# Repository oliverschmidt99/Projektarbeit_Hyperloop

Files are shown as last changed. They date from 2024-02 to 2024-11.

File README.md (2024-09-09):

# Hyperloop

Hyperloop-Projektarbeit an der Hochschule Emden/Leer

## Installiere MATLAB und das IO-Blockset von Speedgoat.

### Linux

#### Installation von Matlab
Lade [Matlab](https://de.mathworks.com/downloads/) herunter. Erstelle ein Verzeichnis an einen beliebigen Ort und Entpacke die Datei und führe die folgenden Befehle aus.

```bash
xhost +SI:localuser:root 
sudo -H ./install 
xhost -SI:localuser:root
```

#### Installation des IO-Blocksets von Speedgoat

Nach der Installation von MATLAB muss das IO-Blockset von Speedgoat installiert werden. Dafür ist es erforderlich, einen Account bei Speedgoat zu erstellen, um Zugriff auf die [Blockset-Dateien](https://www.speedgoat.com/extranet#/Downloads) zu erhalten.

Lade die ZIP-Datei herunter und entpacke sie in dasselbe Verzeichnis, in dem MATLAB installiert wurde.

Anschließend muss in MATLAB über den internen Dokumentennavigator das Installationsverzeichnis geöffnet werden. Um das IO-Blockset zu installieren, führe in der MATLAB-Konsole den folgenden Befehl aus:

```bash
speedgoat_setup
```

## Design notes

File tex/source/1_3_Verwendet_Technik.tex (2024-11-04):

\chapter{Stand der Technik}
\label{chapter:Stand_der_Technik}

Im folgenden Abschnitt werden die verwendeten Bauteile, welche in Kapitel \ref{chapter:Konzept} dargestellt wurden, näher beschrieben.

\section{Antrieb – Golden Motor}
\label{section:Antrieb}

Golden Motor bietet eine Gesamtlösung bestehend aus einem BLDC-Motor und einem Vector-Controller an. Der Controller besitzt eine Schnittstelle für alle notwendigen Steuer- und Kontrollsignale, um den Motor anzutreiben. Die Anschlüsse sowie die grundlegende Funktionsweise werden in den Abschnitten \ref{section:BLDC_Motor} und \ref{section:Vector_Controller} näher erläutert.

\subsection{BLDC Motor}
\label{section:BLDC_Motor}

Der in Abbildung \ref{BLDC_Motor:img:antrieb_motor} dargestellte BLDC-Motor verfügt über eine Leistung von 10 kW und kann optional durch eine Ölkühlung gekühlt werden, was jedoch für das Fahrzeug derzeit nicht relevant ist. Die Drehzahl ist variabel und kann, mittels des Vector Controllers, welcher in Abschnitt \ref{section:Vector_Controller} erklärt wird, zwischen 2.000 und 6.000 U/min eingestellt werden. Das Nenndrehmoment beträgt 26 Nm, während das maximale Drehmoment bei 85 Nm liegt. Der Wirkungsgrad des Motors beträgt 91 \% \cite{Golden_Motor:bldc_motor}.

\pagebreak[1]
\begin{figure}[!ht]
	\begin{center}
		
		\caption{Golden Motor – 10 KW BLDC Motor Liquid Cooled}
		\label{BLDC_Motor:img:antrieb_motor}
	\end{center}
\end{figure}

Die Anschlüsse des Motors sind in Tabelle \ref{BLDC_Motor:tab:pinmapping} aufgelistet. Der Motor verfügt über zwei Hall-Sensor-Kabel, die jeweils drei Hall-Sensoren sowie einen Temperatursensor enthalten. Zusätzlich sind ein GND- und ein +5V-Versorgungsanschluss in den Hall-Sensor-Kabeln integriert. Die Spulen des Motors werden über sechs separate Kabel angeschlossen: U, V und W.
\pagebreak[1]
\begin{table}[!ht]
	\centering
	\caption{Pin Mapping – BLDC-Motor}
	\label{BLDC_Motor:tab:pinmapping}
	\begin{tabular}{lll}
		\hline
		\textbf{Anschluss}          & \textbf{Funktionalität} & \textbf{Farbe} \\ \hline
		\multicolumn{3}{c}{\textbf{Anschluss Adern Motor}}                     \\ \hline
		\multicolumn{1}{l|}{U1}     & Spule 1                 & Gelb           \\
		\multicolumn{1}{l|}{V1}     & Spule 2                 & Grün           \\
		\multicolumn{1}{l|}{W1}     & Spule 3                 & Blau           \\
		\multicolumn{1}{l|}{U2}     & Spule 1                 & Gelb           \\
		\multicolumn{1}{l|}{V2}     & Spule 2                 & Grün           \\
		\multicolumn{1}{l|}{W2}     & Spule 3                 & Blau           \\ \hline
		\multicolumn{3}{c}{\textbf{Motor Hall Kabel 1}}                        \\ \hline
		\multicolumn{1}{l|}{Hall A} & Hall Sensor             & Gelb           \\
		\multicolumn{1}{l|}{Hall B} & Hall Sensor             & Grün           \\
		\multicolumn{1}{l|}{Hall C} & Hall Sensor             & Blau           \\
		\multicolumn{1}{l|}{Temp}   & Temperatur Sensor       & Weiß           \\
		\multicolumn{1}{l|}{+5V}    & Spannungsversorgung     & Rot            \\
		\multicolumn{1}{l|}{GND}    & Masse                   & Schwarz        \\ \hline
		\multicolumn{3}{c}{\textbf{Motor Hall Kabel 2}}                        \\ \hline
		\multicolumn{1}{l|}{Hall A} & Hall Sensor             & Gelb           \\
		\multicolumn{1}{l|}{Hall B} & Hall Sensor             & Grün           \\
		\multicolumn{1}{l|}{Hall C} & Hall Sensor             & Blau           \\
		\multicolumn{1}{l|}{Temp}   & Temperatur Sensor       & Weiß           \\
		\multicolumn{1}{l|}{+5V}    & Spannungsversorgung     & Rot            \\
		\multicolumn{1}{l|}{GND}    & Masse                   & Schwarz        \\ \hline
	\end{tabular}
\end{table}
\pagebreak[4]

\subsubsection*{Funktionsweise}
\label{BLDC_Motor:Funktionsweise}
Ein BLDC-Motor (Brushless DC Motor) unterscheidet sich grundlegend von einem herkömmlichen Gleichstrommotor. Während bei einem traditionellen DC-Motor die Polumschaltung (Kommutierung) mechanisch über Kohlebürsten erfolgt, übernimmt beim BLDC-Motor eine elektronische Steuerung diese Aufgabe. Dadurch entfällt die Notwendigkeit von Kohlebürsten, was den Motor effizienter und langlebiger macht\cite{mathworks:bldc_motor}.
\newpage

\subsection{Vector Controller}
\label{section:Vector_Controller}

Der Motor wird mithilfe eines Vector-Controllers angesteuert, der in Abbildung \ref{Vector_Controller:img:Antrieb_Controller} dargestellt ist. Der Controller hat die Aufgabe, den Motor basierend auf den Eingangssignalen so zu steuern, dass beispielsweise eine gewünschte Drehzahl erreicht wird. Die genaue Funktionsweise des Vector-Controllers wird kurz unter \ref{Vector_Controller:Funktionsweise} erläutert.

Das Pin-Mapping ist in Tabelle \ref{Vector_Controller:tab:pinmapping} aufgeführt. Bei den Steuersignalen muss auf den Spannungsbereich geachtet werden, da der Controller eine Störung meldet, wenn ein Signal außerhalb des zulässigen Bereichs liegt. Dies ist ein integriertes Sicherheitssystem des Controllers. So liegt beispielsweise bei der Bremse das logische Signal bei 0, wenn die Spannung 1 V beträgt. Tritt ein Kabelbruch ein, wird die Spannung am Controller bei 0 V liegen und eine Warnung wird durch ein periodisches Tonsignal ausgegeben.

\begin{figure}[!ht]
	\begin{center}
		
		\caption{Golden Motor – VECTOR 500 Motor Controller}
		\label{Vector_Controller:img:Antrieb_Controller}
	\end{center}
\end{figure}

\begin{table}[!ht]
	\centering
	\caption{Pin Mapping – Vector Controller}
	\label{Vector_Controller:tab:pinmapping}
	\begin{tabular}{lll|l}
		\hline
		\textbf{Anschluss}        & \textbf{Funktionalität} & \textbf{Farbe} & \textbf{U in V} \\ \hline
		\multicolumn{4}{c}{\textbf{Batterie Eingang}}                                          \\ \hline
		\multicolumn{1}{l|}{B+}   & Versorgungsspannung     & RT             & 48 V            \\
		\multicolumn{1}{l|}{B-}   & Masse                   & SW             & 0 V             \\ \hline
		\multicolumn{4}{c}{\textbf{Motor Ausgnag}}                                             \\ \hline
		\multicolumn{1}{l|}{U}    & Spule 1                 & GE             &                 \\
		\multicolumn{1}{l|}{V}    & Spule 2                 & GN             &                 \\
		\multicolumn{1}{l|}{W}    & Spule 3                 & BL             &                 \\ \hline
		\multicolumn{4}{c}{\textbf{Digitale und Analoge I/O}}                                  \\ \hline
		\multicolumn{1}{l|}{5}    & Masse - Bremse          & SW             & 0 V             \\
		\multicolumn{1}{l|}{6}    & Masse                   & SW             & 0 V             \\
		\multicolumn{1}{l|}{6}    & Masse - Tempomat        & SW             & 0 V             \\
		\multicolumn{1}{l|}{7}    & Tempomat                & GR             & 0 V oder 5 V    \\
		\multicolumn{1}{l|}{10}   & elektronisches Schloss  & RS             & 0 V oder 5 V    \\
		\multicolumn{1}{l|}{16}   & Bremse                  & BL\&WS         & 1 V oder 5 V    \\
		\multicolumn{1}{l|}{17}   & Fahrtrichtung           & BR             & 0 V oder 5 V    \\
		\multicolumn{1}{l|}{26}   & Masse                   & SW\&WS         & 0 V             \\
		\multicolumn{1}{l|}{27}   & Geschwindigkeit         & GN\&WS         & 1 V - 4 V       \\
		\multicolumn{1}{l|}{28}   & +5 V                    & RT\&WS         & 5 V             \\ \hline
		\multicolumn{4}{c}{\textbf{Hallsensor Kabel}}                                          \\ \hline
		\multicolumn{1}{l|}{(3)}  & Motor Temperatur        & WS             &                 \\
		\multicolumn{1}{l|}{(11)} & Hall C – Sensor         & BL             &                 \\
		\multicolumn{1}{l|}{(12)} & Hall B – Sensor         & GN             &                 \\
		\multicolumn{1}{l|}{(13)} & Hall A – Sensor         & GE             &                 \\
		\multicolumn{1}{l|}{(14)} & +5 V                    & RT             & 5 V             \\
		\multicolumn{1}{l|}{(21)} & Masse                   & SW             & 0 V             \\ \hline
	\end{tabular}
\end{table}
\pagebreak[4]

\subsubsection*{Funktionsweise}
\label{Vector_Controller:Funktionsweise}
Der Vector-Controller verwendet die Motorsteuerungstechnologie der feldorientierten Regelung (Field-Oriented Control, FOC). Dabei wird die Position des Rotors im Motor mithilfe von Hall-Sensoren ermittelt. Mit der FOC-Technik ist es möglich, das Verhältnis von Drehmoment pro Ampere zu maximieren. Dafür muss der RotorflussVector im rechten Winkel (90 Grad) zum StatorflussVector ausgerichtet sein \cite{Golden_Motor:Vector_Controller}.

\newpage

\section{Echtzeitfähige Steuerung – Speedgoat}
\label{section:speedgoat}

Der Baseline Real-Time Target Machine, wie in Abbildung \ref{speedgoat:img:steuerung_goat} dargestellt, ist ein echtzeitfähiges System, welches von der Firma Speedgoat hergestellt und vertrieben wird. Es wird hauptsächlich in der Entwicklung und beim Testen von komplexen Steuerungs- und Regelungssystemen eingesetzt, bei denen die Echtzeitfähigkeit eine zentrale Rolle spielt.\\ \ \\

\pagebreak[1]
\begin{figure}[!ht]
	\begin{center}
		
		\caption{Speedgoat – Baseline Real-Time Target Machine}
		\label{speedgoat:img:steuerung_goat}
	\end{center}
\end{figure}
\pagebreak[1]

Speedgoat-Systeme integrieren sich nahtlos in Simulink, einer Software von MathWorks, die häufig zur Modellierung und Simulation dynamischer Systeme verwendet wird. Durch eine große Auswahl an I/O-Modulen lassen sich verschiedene Sensoren und Aktuatoren problemlos an die Systeme anschließen.
Echtzeitsysteme von Speedgoat sind Computer, die in der Lage sind, Aufgaben innerhalb festgelegter Zeitintervalle auszuführen. Diese Systeme sind entscheidend für Anwendungen, bei denen die zeitliche Genauigkeit von großer Bedeutung ist, wie beispielsweise bei der Steuerung von Motoren, der Regelung von Prozessen oder der Simulation von physikalischen Systemen.

\pagebreak[1]
\begin{figure}[!ht]
	\begin{center}
		
		\caption{Speedgoat – Ansicht der Modulanschlüsse}
		\label{speedgoat:img:Modulanschlüsse}
	\end{center}
\end{figure}
\pagebreak[1]
In Abbildung \ref{speedgoat:img:Modulanschlüsse} sind die Anschlüsse der I/O-Module des Speedgoat-Systems dargestellt. Die Zuordnung der Module zu den entsprechenden Anschlüssen ist in Tabelle \ref{speedgoat:tab:Module} ersichtlich.

Das Modul IO397-50k kann über ein Sensor-Aktor-Kabel von Phoenix Contact extern angeschlossen werden, wie in Abbildung \ref{IO397_50k:img:Module} dargestellt.
Zusätzlich wird das Modul IO691 mittels eines 9-Pin D-Sub-Steckers angeschlossen.
\pagebreak[1]
\begin{table}[!ht]
	\centering
	\caption{Speedgoat – Anschlüsse der Module}
	\label{speedgoat:tab:Module}
	\begin{tabular}{clll}
		\hline
		\multicolumn{2}{c}{\textbf{I/O Module}} & \multicolumn{1}{c}{\textbf{Name}} & \textbf{Funktion}               \\ \hline
		\multirow{2}{*}{1}                      & \multicolumn{1}{l|}{A}            & IO397-50k         & analog I/O  \\
		                                        & \multicolumn{1}{l|}{B}            & IO397-50k         & digital I/O \\ \hline
		\multirow{2}{*}{2}                      & \multicolumn{1}{l|}{A}            & IO691             & CAN         \\
		                                        & \multicolumn{1}{l|}{B}            & IO691             & CAN         \\ \hline
		\multirow{2}{*}{3}                      & \multicolumn{1}{l|}{A}            & IO397-50k         & analog I/O  \\
		                                        & \multicolumn{1}{l|}{B}            & IO397-50k         & digital I/O \\ \hline
		\multirow{2}{*}{4}                      & \multicolumn{1}{l|}{A}            & IO397-50k         & analog I/O  \\
		                                        & \multicolumn{1}{l|}{B}            & IO397-50k         & digital I/O \\ \hline
	\end{tabular}
\end{table}
\pagebreak[4]

\subsection{I/O-Modul – IO397-50k}
\label{section:IO397_50k}

Das in Abbildung \ref{IO397_50k:img:Module} dargestellte IO397-50k I/O-Modul verfügt über zahlreiche analoge und digitale Ein- und Ausgänge. Die Anschlüsse werden auf Modul A, das die analogen Schnittstellen bereitstellt, und Modul B, welches die digitalen Schnittstellen umfasst, verteilt. Die Anschlussbelegung wird in den Tabellen \ref{IO397_50k:tab:Board_A} und \ref{IO397_50k:tab:Board_B} dargestellt. Die Spannungen der Ein- und Ausgänge können softwaregesteuert angepasst werden \cite{speedgoat:IO397_50k}.

\pagebreak[1]
\begin{figure}[!ht]
	\begin{center}
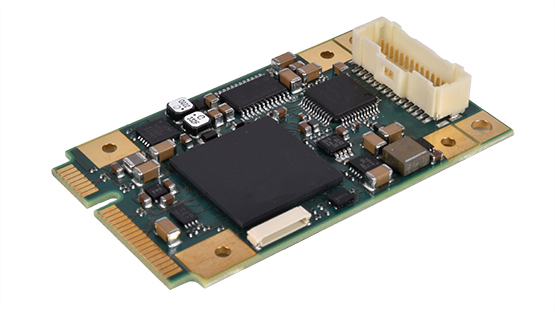
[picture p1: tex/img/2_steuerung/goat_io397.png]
		
		\caption{Speedgoat – I/O Module 397 \cite{speedgoat:IO397_50k}}
		\label{IO397_50k:img:Module}
	\end{center}
\end{figure}
\pagebreak[1]

\subsubsection{Pin Mapping – IO397-50k}

Das Terminal Board A ist für die Verarbeitung analoger Signale konzipiert, sowohl für Eingänge als auch für Ausgänge. Die Tabelle \ref{IO397_50k:tab:Board_A} zeigt das Pin-Mapping von Terminal Board A. Dieses Board verfügt über Anschlüsse für insgesamt vier analoge Eingänge (Pins A1 bis A8) und vier analoge Ausgänge (Pins A9 bis A12). Die Ausgänge sind an einen Digital-zu-Analog-Wandler (DAC) angeschlossen, während die Eingänge mit einem Analog-zu-Digital-Wandler (ADC) verbunden sind.

\pagebreak[1]
\begin{table}[!ht]
	\centering
	\caption{IO397-50k Pin Mapping – Terminal Board A: analog I/O \cite[15]{speedgoat:IO397_50k}}
	\label{IO397_50k:tab:Board_A}
	\begin{tabular}{lll}
		\hline
		\textbf{Pin}             & \textbf{Funktionalität} & \textbf{Type} \\ \hline
		\multicolumn{1}{l|}{A1}  & Analog input 1 +        & ADC           \\
		\multicolumn{1}{l|}{A2}  & Analog input 1 -        & ADC           \\
		\multicolumn{1}{l|}{A3}  & Analog input 2 +        & ADC           \\
		\multicolumn{1}{l|}{A4}  & Analog input 2 -        & ADC           \\
		\multicolumn{1}{l|}{A5}  & Analog input 3 +        & ADC           \\
		\multicolumn{1}{l|}{A6}  & Analog input 3 -        & ADC           \\
		\multicolumn{1}{l|}{A7}  & Analog input 4 +        & ADC           \\
		\multicolumn{1}{l|}{A8}  & Analog input 4 -        & ADC           \\ \hline
		\multicolumn{1}{l|}{A9}  & Analog output 1         & DAC           \\
		\multicolumn{1}{l|}{A10} & Analog output 2         & DAC           \\
		\multicolumn{1}{l|}{A11} & Analog output 3         & DAC           \\
		\multicolumn{1}{l|}{A12} & Analog output 4         & DAC           \\ \hline
		\multicolumn{1}{l|}{A13} & GND                     & GND           \\
		\multicolumn{1}{l|}{A14} & GND                     & GND           \\
		\multicolumn{1}{l|}{A15} & 0 V                     & 0 V           \\
		\multicolumn{1}{l|}{A16} & 5 V DC                  & 5 V DC        \\
		\multicolumn{1}{l|}{A17} & GND                     & GND           \\
		\multicolumn{1}{l|}{SH}  & SH                      & Shielding     \\ \hline
	\end{tabular}
\end{table}
\pagebreak[1]

Terminal Board B hingegen bietet eine flexible Konfiguration für digitale Ein- und Ausgänge. Die Tabelle \ref{IO397_50k:tab:Board_B} zeigt das Pin Mapping von Terminal Board B. Die Pins B3 bis B16 sind für konfigurierbare I/O-Funktionalitäten ausgelegt und nutzen TTL-Signale (Transistor-Transistor-Logik), was sie besonders für schnelle digitale Schaltvorgänge geeignet macht. Dieses Board ermöglicht es, die Anschlüsse flexibel zu nutzen, je nach den Anforderungen der Applikation. Auch hier gibt es mehrere Spannungs- und Ground-Anschlüsse, sowie eine Abschirmung (Shielding) für das M12-Kabel, um elektromagnetische Störungen zu minimieren.

\pagebreak[1]
\begin{table}[!ht]
	\centering
	\caption{IO397-50k Pin Mapping – Terminal Board B: analog I/O \cite[15]{speedgoat:IO397_50k}}
	\label{IO397_50k:tab:Board_B}
	\begin{tabular}{lll}
		\hline
		\textbf{Pin}             & \textbf{Funktionalität} & \textbf{Type} \\ \hline
		\multicolumn{1}{l|}{B1}  & 0 V                     & 0 V           \\
		\multicolumn{1}{l|}{B2}  & 5 V DC                  & 5 V DC        \\ \hline
		\multicolumn{1}{l|}{B3}  & I/O 0                   & IN/OUT        \\
		\multicolumn{1}{l|}{B4}  & I/O 1                   & IN/OUT        \\
		\multicolumn{1}{l|}{B5}  & I/O 2                   & IN/OUT        \\
		\multicolumn{1}{l|}{B6}  & I/O 3                   & IN/OUT        \\
		\multicolumn{1}{l|}{B7}  & I/O 4                   & IN/OUT        \\
		\multicolumn{1}{l|}{B8}  & I/O 5                   & IN/OUT        \\
		\multicolumn{1}{l|}{B9}  & I/O 6                   & IN/OUT        \\
		\multicolumn{1}{l|}{B10} & I/O 7                   & IN/OUT        \\
		\multicolumn{1}{l|}{B11} & I/O 8                   & IN/OUT        \\
		\multicolumn{1}{l|}{B12} & I/O 9                   & IN/OUT        \\
		\multicolumn{1}{l|}{B13} & I/O 10                  & IN/OUT        \\
		\multicolumn{1}{l|}{B14} & I/O 11                  & IN/OUT        \\
		\multicolumn{1}{l|}{B15} & I/O 12                  & IN/OUT        \\
		\multicolumn{1}{l|}{B16} & I/O 13                  & IN/OUT        \\\hline
		\multicolumn{1}{l|}{B17} & GND                     & GND           \\
		\multicolumn{1}{l|}{B18} & SH                      & Shielding     \\ \hline
	\end{tabular}
\end{table}
\pagebreak[4]

\subsubsection{IO397-50k – Konfigurieren}
\label{Simulink:IO397_50k_Konfigurieren}

In dem Driver Block, wie in Abbildung \ref{IO397_50k_Konfigurieren:img:Driver_Block} gezeigt, können an dem Pull-Widerstand des I/O-Moduls verschiedene Spannungen eingestellt werden. Zur Auswahl stehen:\\
\begin{itemize}
	\item Pull-up 3,3 V
	\item Weak Pull-up 5,0 V
	\item Pull-down
	\item Floating
\end{itemize}

\pagebreak[1]
\begin{figure}[!ht]
	\begin{center}
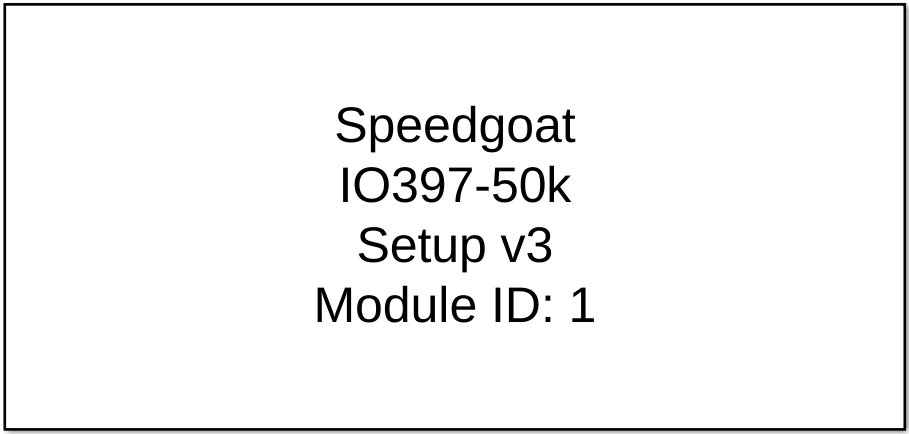
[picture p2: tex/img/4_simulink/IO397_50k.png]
		
		\caption{Simulink – Driver Block – IO397-50k}
		\label{IO397_50k_Konfigurieren:img:Driver_Block}
	\end{center}
\end{figure}
\pagebreak[1]

Pull-Widerstände werden verwendet, um klare digitale Schaltzustände zu gewährleisten. Es gibt drei verschiedene Zustände: \frqq High\flqq\ entspricht \frqq logisch 1\flqq, Low entspricht \frqq logisch 0\flqq, \frqq Floating\flqq\ hat die Bedeutung, dass der Widerstand nicht an \frqq GND\flqq\ oder an einer Spannung angeschlossen ist. Somit ist der Widerstand hochohmig. Die Zustände zu den Einstellungen sind in der Tabelle \ref{IO397_50k_Konfigurieren:tab:Reaktionszeit} aufgeführt.
In Abbildung \ref{IO397_50k_Konfigurieren:img:TTL_IO_Interface} ist im rot markierten Bereich der Pull-Widerstand mit 4,7 k$\Omega$ an einen 47-$\Omega$-Widerstand am I/O-Anschluss angeschlossen. Der Pull-Widerstand kann, wie bereits erwähnt, konfiguriert werden. Dabei wird intern am Pull-Widerstand entweder eine Spannung von 3,3 V, 5 V, GND oder kein Kontakt, also Floating (hochohmig), geschaltet.

\pagebreak[1]
\begin{figure}[!ht]
	\begin{center}
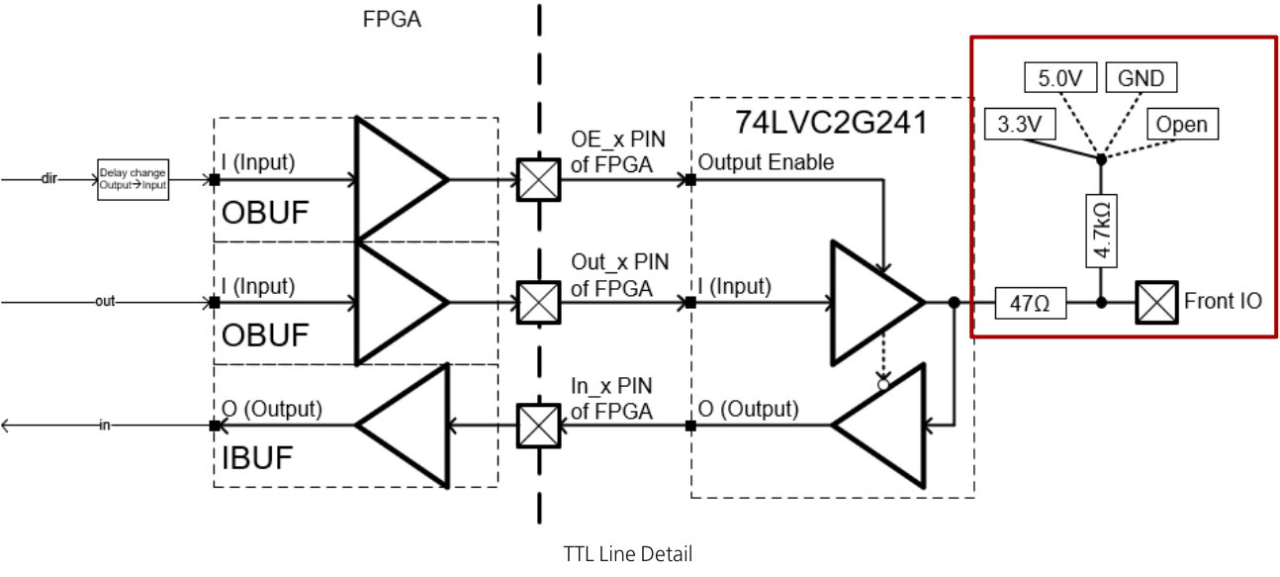
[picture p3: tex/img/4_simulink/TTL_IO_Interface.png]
		
		\caption{Speedgoat – TTL I/O Interface – IO397-50k \cite[12]{speedgoat:IO397_50k}}
		\label{IO397_50k_Konfigurieren:img:TTL_IO_Interface}
	\end{center}
\end{figure}
\pagebreak[2]

Bei der Einstellung auf 3,3 V oder 5 V fungiert der Widerstand als Pull-up-Widerstand. Bei der Pull-down-Konfiguration liegt am Widerstand Ground (GND) an.

In Tabelle \ref{IO397_50k_Konfigurieren:tab:Reaktionszeit} können die Reaktionszeiten der digitalen Ausgänge verglichen werden. Bei der Einstellung \frqq Weak Pull-up 5,0 V\flqq\ bedeutet \frqq weak\flqq, dass das Ausgangssignal eine längere Anstiegszeit hat. In Abbildung \ref{IO397_50k_Konfigurieren:img:Pull_Widerstande} sind die Reaktionszeiten dargestellt.

\pagebreak[1]
\begin{table}[!ht]
	\centering
	\caption{Simulink – Pull-Widerstand – Reaktionszeit}
	\label{IO397_50k_Konfigurieren:tab:Reaktionszeit}
	\begin{tabular}{lccc}
		\hline
		\multicolumn{1}{c}{\multirow{2}{*}{\textbf{Einstellung}}} & \multicolumn{1}{c}{\multirow{2}{*}{\textbf{Logischer Zustand}}} & \multicolumn{2}{c}{\textbf{Reaktionszeit der Ausgänge}}           \\ \cline{3-4}
		\multicolumn{1}{c}{}                                      & \multicolumn{1}{c}{}                                            & Anstieg                                                 & Abfall  \\ \hline
		\multicolumn{1}{l|}{Pull-up 3,3V}                         & I/O = 1                                                         & Schnell                                                 & Schnell \\
		\multicolumn{1}{l|}{weak pull-up 5,0V}                    & I/O = 1                                                         & Langsam                                                 & Schnell \\
		\multicolumn{1}{l|}{Pull-down}                            & I/O = 0                                                         & Schnell                                                 & Langsam \\
		\multicolumn{1}{l|}{Floating}                             & I/O = 0 - 1                                                     & -                                                       & -       \\ \hline
	\end{tabular}
\end{table}
\pagebreak[1]

\pagebreak[1]
\begin{figure}
	\begin{minipage}{0.8\textwidth}
		\centering
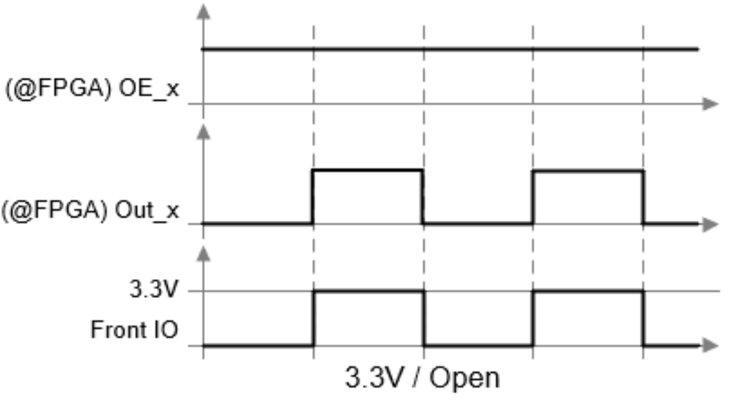
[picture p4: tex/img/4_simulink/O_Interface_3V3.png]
		
		\caption*{Pull-up-Widerstand 3,3 V}
	\end{minipage}
	\begin{minipage}{0.8\textwidth}
		\centering
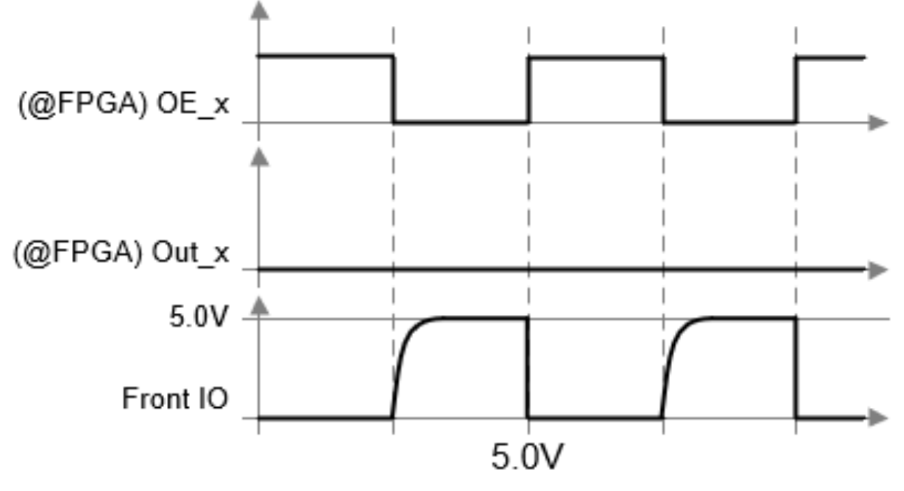
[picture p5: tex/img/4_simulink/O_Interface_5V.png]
		
		\caption*{Weak Pull-up-Widerstand 5 V}
	\end{minipage}
	\begin{minipage}{0.8\textwidth}
		\centering
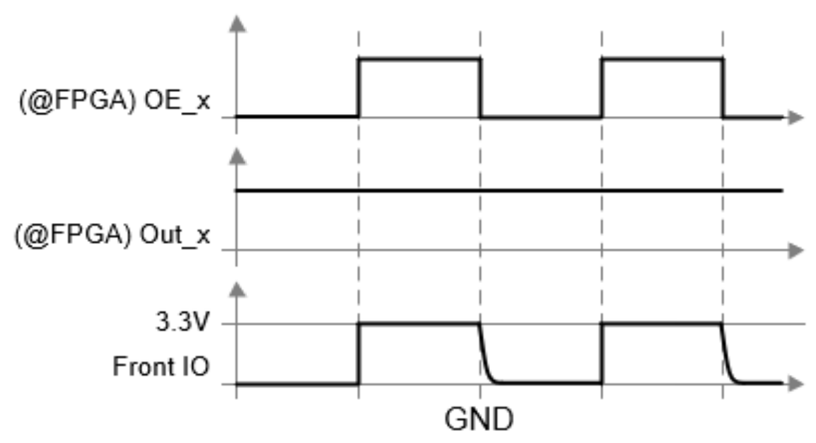
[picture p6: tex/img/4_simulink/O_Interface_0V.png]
		
		\caption*{Pull-down-Widerstand GND}
	\end{minipage}
	\caption{Simulink – Pull-Widerstände – IO397-50k \cite[12]{speedgoat:IO397_50k}}
	\label{IO397_50k_Konfigurieren:img:Pull_Widerstande}
\end{figure}
\pagebreak[4]

\newpage
\subsection{I/O-Modul – IO691}
\label{section:IO691}

Das IO691 I/O-Modul bietet eine intelligente CAN-Schnittstelle mit zwei Kanälen, die sowohl flexible Datenrate CAN (CAN FD) als auch High-Speed CAN (CAN HS) unterstützen. Es ist kompatibel mit CAN 2.0A/B-Netzwerken und unterstützt SAE J1939 sowie ASAM XCP für Bypassing. Alle Signale sind über 9-polige D-Sub-Front-CAN-Anschlüsse zugänglich \cite[4]{speedgoat:IO691}.

\pagebreak[1]
\begin{figure}[!ht]
	\begin{center}
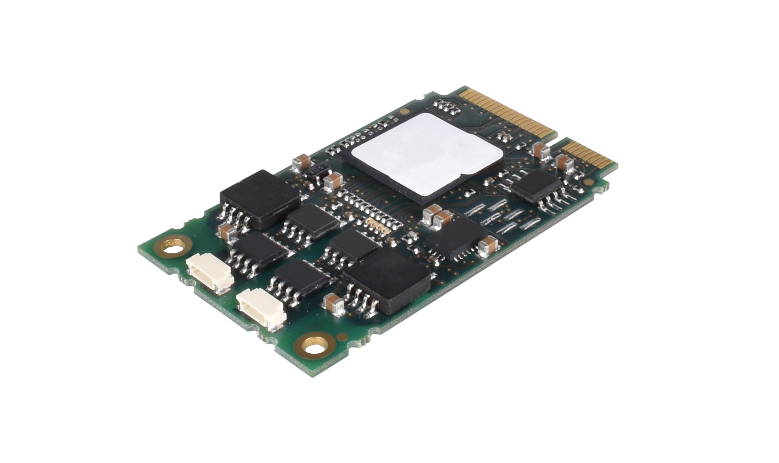
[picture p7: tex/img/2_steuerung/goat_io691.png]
		
		\caption{Speedgoat – I/O Module 691 \cite{speedgoat:IO691}}
		\label{img_2_2:goat:IO691}
	\end{center}
\end{figure}
\pagebreak[4]

\subsubsection{Pin Mapping –  IO691}

\pagebreak[1]
\begin{table}[!ht]
	\centering
	\caption{IO691 Pin Mapping}
	\label{speedgoat:IO691}
	\begin{tabular}{lllc}
		\hline
		\textbf{Pin}            & \textbf{Farbe} & \textbf{An Sensor} & \textbf{DB9 Connector A/B, Signal} \\ \hline
		\multicolumn{1}{l|}{1}  & Braun          & PIN 2 -  Weiß      & Vcc                                \\
		\multicolumn{1}{l|}{2}  & Rot            & PIN 5 -  Grau      & CAN-low                            \\
		\multicolumn{1}{l|}{3}  & Orange         & PIN 3 -  Blau      & GND                                \\
		\multicolumn{1}{l|}{4}  & Gelb           &                    & -                                  \\
		\multicolumn{1}{l|}{5}  & Grün           &                    & -                                  \\
		\multicolumn{1}{l|}{6}  & Blau           & PIN 3 -  Blau      & GND                                \\
		\multicolumn{1}{l|}{7}  & Viollet        & PIN 4 -  Schwarz   & CAN-high                           \\
		\multicolumn{1}{l|}{8}  & Grau           &                    & -                                  \\
		\multicolumn{1}{l|}{9}  & Schwarz        &                    & -                                  \\
		\multicolumn{1}{l|}{SH} &                & PIN 1 - Braun      & Shield                             \\ \hline
	\end{tabular}
\end{table}
\pagebreak[1]

\subsubsection{IO691 Module konfigurieren}
\label{Simulink:IO691_Konfigurieren}

Im \frqq Driver Block\flqq, siehe Abbildung \ref{IO691_Konfigurieren:img:Driver_Block}, können die \frqq CAN Channels\flqq\ 1 und 2 konfiguriert werden. Wie bereits in Abschnitt \ref{section:IO691} erwähnt, lässt sich der Protokollmodus jedes Kanals separat einstellen, wobei zwischen \frqq CAN HS\flqq, \frqq CAN FD\flqq\ und \frqq Disable\flqq\ gewählt werden kann. Dabei entspricht \frqq CAN HS\flqq\ der Norm ISO 11898-2 und \frqq CAN FD\flqq\ der Norm ISO 11898-1 \cite[4]{speedgoat:IO691}.

\pagebreak[1]
\begin{figure}[!ht]
	\begin{center}
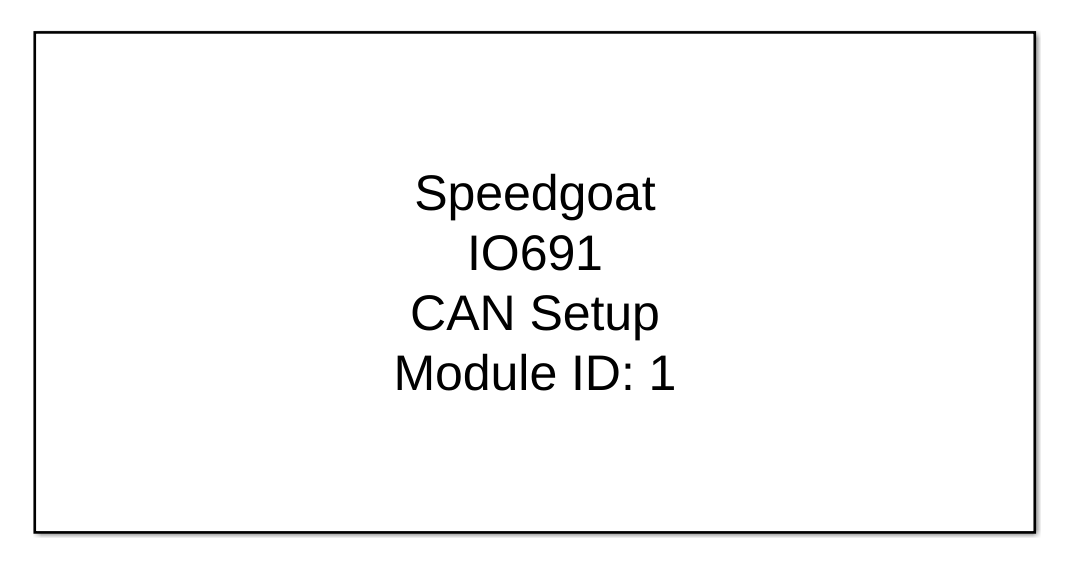
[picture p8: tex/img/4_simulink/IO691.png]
		
		\caption{Simulink – Driver Block – I/O Module 691 \cite{speedgoat:IO691}}
		\label{IO691_Konfigurieren:img:Driver_Block}
	\end{center}
\end{figure}
\pagebreak[1]

Die \frqq Initialization\flqq- und \frqq Termination\flqq-CAN-Nachrichten können individuell angepasst werden. Im nachfolgenden Matlab-Skript (\ref{IO691_Konfigurieren:code:Driver_Block}) werden die Variablen \frqq initCAN\flqq\ und \frqq termCAN\flqq\ definiert.

\pagebreak[4]
\begin{lstlisting}[language=Matlab, caption={Initialization and Termination Structure} \cite{speedgoat:IO691:CAN_Message}\label{IO691_Konfigurieren:code:Driver_Block}]
% create Initialization structure
initCAN.Channel     = 1;
initCAN.Protocol    = 'CAN-FD';         % 'CAN' or 'CAN-FD'
initCAN.BRS         = 1;                % 0 or 1
initCAN.Type        = 'Standard';       % 'Standard' or 'Extended'
initCAN.Identifier  = 99;               % ID must be double
initCAN.Data        = [8 8 8 8 8 8 8 8];
initCAN.Pause       = 0.05;

% create Termination structure
termCAN.Channel     = 1;
termCAN.Protocol    = 'CAN-FD';         % 'CAN' or 'CAN-FD'
termCAN.BRS         = 1;                % 0 or 1
termCAN.Type        = 'Extended';       % 'Standard' or 'Extended'     
termCAN.Identifier  = double(0xFFF);    % ID must be double
termCAN.Data        = [1 1 1 1 1 1 1 1];
termCAN.Pause       = 0.05

\end{lstlisting}
\pagebreak[1]

Die Baudrate kann in zwei Kategorien unterteilt werden: \frqq Nominal Baud Rate\flqq\ und \frqq Data Baud Rate\flqq. Wenn im \frqq CAN Channels\flqq-Menü der Modus \frqq CAN FD\flqq\ ausgewählt wird, können beide Baudraten konfiguriert werden. Im Modus \frqq CAN HS\flqq\ ist die Einstellung der \frqq Nominal Baud Rate\flqq\ ausschließlich möglich. \\
Es können entweder die voreingestellten Baudraten verwendet oder eigene Werte über ein Array [BRP, SJW, TSEG1, TSEG2] konfiguriert werden, deren Elemente im Folgenden kurz erläutert werden, siehe Tabelle \ref{IO691_Konfigurieren:tab:Baudraten}.

\pagebreak[1]
\begin{table}[!ht]
	\centering
	\caption{Simulink – Baudraten Parameter }
	\label{IO691_Konfigurieren:tab:Baudraten}
	\begin{tabular}{ll}
		\hline
		\multicolumn{1}{c}{\textbf{Abkürzung}} & \multicolumn{1}{c}{\textbf{Bedeutung}} \\ \hline
		\multicolumn{1}{l|}{BRP}               & Bit Rate Prescaler                     \\
		\multicolumn{1}{l|}{SJW}               & Synchronization Jump Width             \\
		\multicolumn{1}{l|}{TSEG1}             & Time Segment 1                         \\
		\multicolumn{1}{l|}{TSEG2}             & Time Segment 2                         \\ \hline
	\end{tabular}
\end{table}
\pagebreak[1]

Die sogenannte \frqq CAN Nominal Bit Time\flqq, wie in Abbildung \ref{IO691_Konfigurieren:img:Baudrate} dargestellt, besteht aus vier Segmenten: dem \frqq Sync Segment\flqq, dem \frqq Propagation Segment\flqq, dem \frqq Phase Buffer Segment 1\flqq\ und dem \frqq Phase Buffer Segment 2\flqq.
Das \frqq Sync Segment\flqq\ dient zur Synchronisation der Knoten auf dem Bus und hat eine Länge von genau einem Zeitquantum.
Im \frqq Propagation Segment\flqq\ werden die physikalischen Verzögerungen im Busnetzwerk ausgeglichen \cite[1]{microchip:CANModule}.\\
Im \frqq Phase Buffer Segment 1\flqq\ werden positive Phasenfehler kompensiert, und das Segment kann während der Resynchronisation verlängert werden. Im \frqq Phase Buffer Segment 2\flqq\ hingegen werden negative Phasenfehler kompensiert, und das Segment kann während der Resynchronisation verkürzt werden.\\ \ \\

\frqq BRP\flqq\ ist ein Parameter, der das Zeitquant $t_q$ festlegt, siehe Gleichung \ref{eq:tq}.
Der \frqq SJW\flqq\ ist ein Parameter, der die Länge von \frqq TSEG1\flqq\ verlängern und die Länge von \frqq TSEG2\flqq\ verkürzen kann, um die Synchronisation zwischen den Knoten zu gewährleisten, dabei darf \frqq SJW\flqq\ kleiner oder gleich groß \frqq TSEG2\flqq\ sein \cite{speedgoat:IO691:CAN_Message}.

Der Sample Point (SP) ist der Punkt innerhalb eines CAN-Bits, an dem die tatsächliche Datenabtastung stattfindet. Dieser Punkt kann durch das Verhältnis zwischen \frqq TSEG1\flqq\ und \frqq TSEG2\flqq\ angepasst werden.

\pagebreak[1]
\begin{figure}[!ht]
	\begin{center}
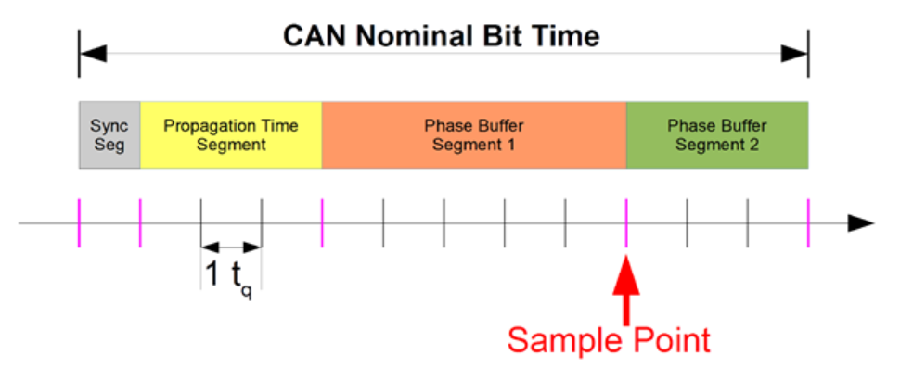
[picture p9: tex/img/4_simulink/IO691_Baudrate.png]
		
		\caption{Simulink – Baudrate – I/O Module 691 \cite{speedgoat:IO691:CAN_Message}}
		\label{IO691_Konfigurieren:img:Baudrate}
	\end{center}
\end{figure}
\pagebreak[1]

Mit den weiteren Gleichungen können die Zeiten innerhalb der \frqq CAN Nominal Bit Time\flqq\ ermittelt werden.
\begin{align}
	\label{eq:tq}
	t_{q}   & = \frac{BRP}{CAN_{Clk}} \\
	t_{BS1} & = t_{q}  \cdot TSEG1    \\
	t_{BS2} & = t_{q}  \cdot TSEG2
\end{align}

\begin{align}
	\begin{split}
		NominalBitTime & = t_{q} + t_{BS1} + t_{BS2}        \\
		               & = t_{q}  \cdot (1 + TSEG1 + TSEG2)
	\end{split}
\end{align}

\begin{align}
	CAN_{Baudrate} & = \frac{1}{NominalBitTime}
\end{align}

\begin{align}
	\begin{split}
		SP & = \frac{(1 + TSEG1)}{(1 + TSEG1 + TSEG2)} \\
		   & = \frac{(t_q + t_{BS1})}{NominalBitTime}
	\end{split}
\end{align}

Am CAN-Bus ist es wichtig, an beiden Enden Abschlusswiderstände von 120 $\Omega$ zu installieren. Diese Widerstände verhindern Reflexionen von Signalen, die auf der Leitung entstehen können, wenn die Impedanz des Busses nicht korrekt abgestimmt ist.\\
Reflexionen können das ursprüngliche Signal beeinträchtigen und zu Fehlern in der Datenkommunikation führen. Die Abschlusswiderstände gewährleisten eine angepasste Impedanz und minimieren somit die Wahrscheinlichkeit von Signalreflexionen \cite{speedgoat:IO691:CAN_Message}.

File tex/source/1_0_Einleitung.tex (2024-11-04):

\chapter{Einleitung}
\label{chapter:Einleitung}

\section{Motivation der Hyperloop Technologie}
\label{section:Motivation}

Der Hyperloop ist ein innovatives Transportkonzept, das eine ökonomische, klimafreundliche und schnellere Alternative zu herkömmlichen Verkehrsmitteln wie Lastkraftwagen, Zügen und Flugzeugen bietet.\\
\pagebreak[3]
\begin{figure}[!ht]
	\begin{center}
		
		\caption{Hyperloop der Hochschule Emden-Leer}
		\label{img_1_1:strecke}
	\end{center}
\end{figure}
\pagebreak[4]
Derzeit stehen herkömmlichen Transportmitteln zwei wesentliche Hindernisse im Weg, um Personen und Güter schnell und emissionsarm zu befördern. Zum einen der hohe Luftwiderstand, der bei hohen Geschwindigkeiten den Energieverbrauch stark erhöht.\\
Der Hyperloop löst diese Probleme, indem er Güter und Personen in einem Fahrzeug, das sich in einer fast Vakuumröhre bewegt, wie in Abbildung \ref{img_1_1:strecke} dargestellt ist.

%%%%%%%%%%%%%%%%%%%%%%%%%%%%%%%%%%%%%%%%%%%%%%%%%%%%%%%%%%%%%%%%%%%%%%%%%%%%%%%%%%%%
%%%%%%%%%%%%%%%%%%%%%%%%%%%%%%%%%%%%%%%%%%%%%%%%%%%%%%%%%%%%%%%%%%%%%%%%%%%%%%%%%%%%
%%%%%%%%%%%%%%%%%%%%%%%%%%%%%%%%%%%%%%%%%%%%%%%%%%%%%%%%%%%%%%%%%%%%%%%%%%%%%%%%%%%%
%%%%%%%%%%%%%%%%%%%%%%%%%%%%%%%%%%%%%%%%%%%%%%%%%%%%%%%%%%%%%%%%%%%%%%%%%%%%%%%%%%%%
%%%%%%%%%%%%%%%%%%%%%%%%%%%%%%%%%%%%%%%%%%%%%%%%%%%%%%%%%%%%%%%%%%%%%%%%%%%%%%%%%%%%
%%%%%%%%%%%%%%%%%%%%%%%%%%%%%%%%%%%%%%%%%%%%%%%%%%%%%%%%%%%%%%%%%%%%%%%%%%%%%%%%%%%%

\subsection*{Institute of Hyperloop Technology}
\label{section:IHT}

%Die Hochschule Emden/Leer hat im Jahr 2021 das Institut für Hyperloop-Technologie (IHT) gegründet, um aktiv an der Forschung zu dieser zukunftsweisenden Technologie teilzunehmen.

Im Rahmen dieser Forschung-arbeit, -projekt wurde an der Hochschule Emden eine Teststrecke mit einer Länge von 27 Metern errichtet (siehe Abbildung \ref{img_1_1:strecke}). Auf dieser Strecke soll das Fahrzeug (Cargo-Pod) unter realistischen Bedingungen getestet und weiterentwickelt werden.
Die Teststrecke besteht aus einem Schienensystem und einem Linearmotor.\\
Die Forschung des \frqq Institute of Hyperloop Technology\flqq, fokuziert sich auf die Güterbeförderung.
\newpage

\section{Aufgabenstellung}
\label{section:Aufgabenstellung}
Das Ziel dieses Projektes ist die Entwilckung eines Hyperloop-Fahrzeuges, das mit einer Batterie und einem Motor betrieben wird. Für die Steuerung des Fahrzeugs wurde ein echtzeitfähiges Steuerungsystem der Firma Speedgoat vorgeben, welches in Abschnitt \ref{section:speedgoat} vertiefend erläutert wird.\\ \ \\

Im Rahmen des Projekts wird ein Fahrzeug (Pod) für den Hyperloop mit einer Bordspannung von 48 V konzipiert. Ziel ist es, die Realisierbarkeit dieser Spannung zu überprüfen und umzusetzen. Dazu gehören die Planung und Simulierung, die Integration der erforderlichen Sensorik sowie die Beschaffung der notwendigen Bauteile. Die Logik- und Signalverarbeitung wird, mithilfe von Simulink, auf dem echtzeitfähigen Speedgoat-System durchgeführt.
Die Steuerung erfolgt über Simulink, ein Modul von MATLAB, und beinhaltet die Erfassung von Position und Beschleunigung des Fahrzeuges. Der Motor wird über ein zusätzliches Steuergerät angesteuert. Die Steuerung soll in Form einer Automatensteuerung umgesetzt werden.
Die Verdrahtung des Pods wird entsprechend der Bordspannung von 48 V ausgelegt. Hierfür wird mit der Software QElectroTech ein Schaltplan (siehe Anhang \ref{Anhang:Schaltplan}) erstellt.
Alle erforderlichen Bauteile für die Umsetzung der Bordspannung, die Verdrahtung und die Sensorik müssen beschafft werden.\\
Textergebnisse und Inbetriebnahme entfallen.

%%%%%%%%%%%%%%%%%%%%%%%%%%%%%%%%%%%%%%%%%%%%%%%%%%%%%%%%%%%%%%%%%%%%%%%%%%%%%%%%%%%%
%%%%%%%%%%%%%%%%%%%%%%%%%%%%%%%%%%%%%%%%%%%%%%%%%%%%%%%%%%%%%%%%%%%%%%%%%%%%%%%%%%%%
%%%%%%%%%%%%%%%%%%%%%%%%%%%%%%%%%%%%%%%%%%%%%%%%%%%%%%%%%%%%%%%%%%%%%%%%%%%%%%%%%%%%
%%%%%%%%%%%%%%%%%%%%%%%%%%%%%%%%%%%%%%%%%%%%%%%%%%%%%%%%%%%%%%%%%%%%%%%%%%%%%%%%%%%%
%%%%%%%%%%%%%%%%%%%%%%%%%%%%%%%%%%%%%%%%%%%%%%%%%%%%%%%%%%%%%%%%%%%%%%%%%%%%%%%%%%%%
%%%%%%%%%%%%%%%%%%%%%%%%%%%%%%%%%%%%%%%%%%%%%%%%%%%%%%%%%%%%%%%%%%%%%%%%%%%%%%%%%%%%

\section{Aufbau der Projektdokumentation}
\label{section:Aufbau}

Die Projektdokumentation beginnt mit einer Einführung in die Hyperloop-Technologie und der Aufgabenstellung dieses Projekts, die die Motivation und Zielsetzungen erläutern. Es wird dargelegt, warum der Hyperloop als innovative, umweltfreundliche Transportlösung eine wichtige Alternative zu bestehenden Systemen darstellt und welche spezifischen Herausforderungen und Ziele mit der Entwicklung eines funktionsfähigen Prototyps verbunden sind.

Im weiteren Verlauf wird das grundlegende Fahrzeugkonzept vorgestellt. Dabei wird beschrieben, wie die verschiedenen Baugruppen miteinander verbunden sind und welche Rolle das zentrale Steuerungssystem von Speedgoat übernimmt. Auch die verwendeten Sensoren und deren Einbindung in das Gesamtsystem werden erläutert.

Der Dokumentationsteil zur Implementierung zeigt die technische Realisierung der Steuerung und der elektrischen Verdrahtung des Fahrzeugs. Die Erstellung des Schaltplans, die Konfiguration der Steuerlogik sowie die detaillierte Beschreibung der Automatik- und manuellen Steuerungsmodi geben Einblicke in die Funktionsweise und den Aufbau des Systems. Ergänzend wird die Integration der Distanzmessung beschrieben, die eine präzise Positionsermittlung innerhalb der Teststrecke ermöglicht.

Abschließend fasst die Konklusion die Ergebnisse der Projektarbeit zusammen und gibt Hinweise auf mögliche zukünftige Entwicklungen. Hierbei wird auch die Offenheit der Systemarchitektur betont, die eine flexible Weiterentwicklung ermöglicht..

%%%%%%%%%%%%%%%%%%%%%%%%%%%%%%%%%%%%%%%%%%%%%%%%%%%%%%%%%%%%%%%%%%%%%%%%%%%%%%%%%%%%
%%%%%%%%%%%%%%%%%%%%%%%%%%%%%%%%%%%%%%%%%%%%%%%%%%%%%%%%%%%%%%%%%%%%%%%%%%%%%%%%%%%%
%%%%%%%%%%%%%%%%%%%%%%%%%%%%%%%%%%%%%%%%%%%%%%%%%%%%%%%%%%%%%%%%%%%%%%%%%%%%%%%%%%%%
%%%%%%%%%%%%%%%%%%%%%%%%%%%%%%%%%%%%%%%%%%%%%%%%%%%%%%%%%%%%%%%%%%%%%%%%%%%%%%%%%%%%
%%%%%%%%%%%%%%%%%%%%%%%%%%%%%%%%%%%%%%%%%%%%%%%%%%%%%%%%%%%%%%%%%%%%%%%%%%%%%%%%%%%%
%%%%%%%%%%%%%%%%%%%%%%%%%%%%%%%%%%%%%%%%%%%%%%%%%%%%%%%%%%%%%%%%%%%%%%%%%%%%%%%%%%%%

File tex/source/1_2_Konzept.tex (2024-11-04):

\chapter{Konzept}
\label{chapter:Konzept}

Im Folgenden wird der Aufbau des Fahrzeugs erklärt und welche Sensoren verbaut werden. Dabei übernimmt das Steuerungs- und Datenerfassungskonzept von Speedgoat eine zentrale Rolle.\\
\pagebreak[1]
\begin{figure}[!ht]
	\begin{center}
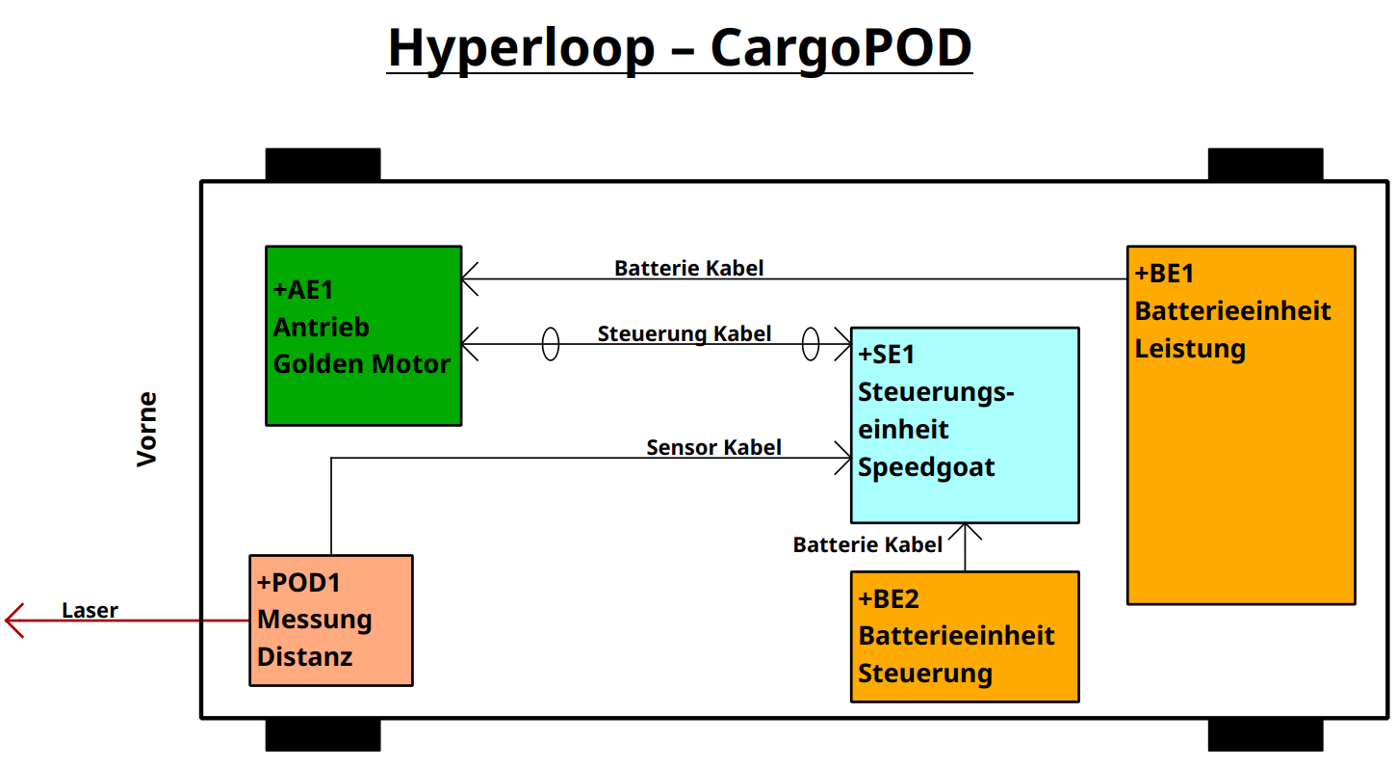
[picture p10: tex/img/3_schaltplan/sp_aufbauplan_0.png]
		
		\caption{Konzept – Aufbauplan des Fahrzeugs}
		\label{img_1_1:Konzept:0}
	\end{center}
\end{figure}
\pagebreak[1]
Wie in Abbildung \ref{img_1_1:Konzept:0} dargestellt, werden die Baugruppen des Fahrzeugs an verschiedenen Stellen miteinander verbunden. Dabei übernimmt die Steuereinheit (+SE1) eine zentrale Rolle. Mit der echtzeitfähigen Steuerung von Speedgoat werden alle digitalen und analogen Ein- und Ausgangssignale gesteuert, einschließlich der Distanzmessung. Die Distanzmessung ist für die Positions- und Geschwindigkeitsermittlung notwendig. Die Steuereinheit (+SE1) wird von der Batterieeinheit (+BE2) mit Energie versorgt.\\
Der Antrieb (+AE1) erfolgt über einen BLDC-Motor. Dieser wird mittels eines zusätzlichen Steuergeräts, einem Vector-Controller, angesteuert. Für die Energieversorgung des Antriebs wird eine Leistungsbatterie (+BE1) verwendet.

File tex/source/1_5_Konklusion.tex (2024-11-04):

\chapter{Konklusion}

In dieser Projektarbeit wurde erfolgreich ein funktionsfähiges Fahrzeug für den Hyperloop-Prototyp entwickelt und dessen Aufbau sowie die Steuerung detailliert beschrieben. Die Implementierung umfasste mehrere wesentliche Schritte: Von der Erstellung eines Schaltplans für die elektrische Verdrahtung über die Integration der Sensorik bis hin zur Programmierung und Simulation der Steuerungslogik.

Die Implementierung der Steuerung erfolgte über ein Speedgoat-System, das Echtzeitsteuerung ermöglicht. Die Simulation der Steuerungslogik in Simulink stellte sicher, dass das Fahrzeug sowohl im manuellen als auch im automatischen Modus betrieben werden kann. Im manuellen Modus kann der Benutzer das Fahrzeug vorwärts und rückwärts fahren lassen, während der automatische Modus das Fahrzeug beschleunigt und bei Annäherung an das Streckenende abbremst. Zudem wurde die Distanzmessung durch einen alternativen Sensor kostengünstig und zuverlässig realisiert, was die Positionierung des Fahrzeugs in der Röhre ermöglicht.

Die Wahl der Bauteile, wie des BLDC-Motors und der IO-Module, sowie die Verdrahtungskonventionen wurden sorgfältig dokumentiert und implementiert, um eine sichere und stabile Betriebsumgebung zu gewährleisten. Die entwickelten Endschnittstellen bieten eine Grundlage für zukünftige Erweiterungen und Testdurchläufe.

Zukünftige Arbeiten könnten darauf abzielen, das Fahrzeug unter realistischen Bedingungen zu testen, um das Zusammenspiel von Steuerung und Sensorik weiter zu optimieren. Die durchgeführten Implementierungen und die offene Architektur des Systems bieten somit eine flexible Basis für die Weiterentwicklung des Hyperloop-Konzepts und die Erforschung einer innovativen, energieeffizienten Transportlösung.

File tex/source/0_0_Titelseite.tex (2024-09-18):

\begin{titlepage}

	\vspace{-0.5cm}
	\hspace{-3.0cm}
	% \hspace{-2.0cm}
	\begin{tabular}{p{8.0cm} p{8.0cm}}
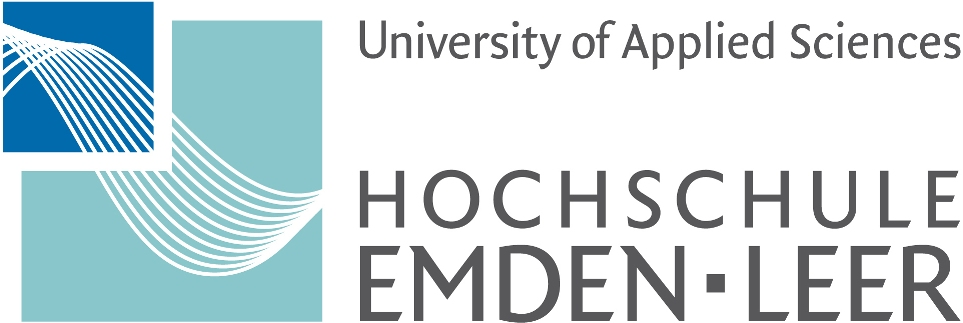
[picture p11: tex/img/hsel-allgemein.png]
		 &
		\parbox[b]{8.0cm}{
		{\large 	Fachbereich Technik }                            \\
		{\large 	Abteilung Elektrotechnik und Informatik }
		}                                                         \\
		\\
		\hline
	\end{tabular}
	%
	\begin{center}

		\vspace{2.5cm}
		\LARGE{\textsc{
				Entwicklung eines Fahrzeuges für den Hyperloop\\
				(Steuerung und Schaltplan)
			}}\\

		\vspace{2cm}
		\LARGE{\textsc{
				{Projektarbeit}
			}}\\
		\large
		Studiengang Elektrotechnik

		\vspace{2cm}
		\large
		Vorgelegt von\\ Oliver Schmidt\\ Studiengang Elektrotechnik\\ Matr. Nr. 7023462

		\vspace{1cm}
		Emden, \today

		\vspace{2.5cm}
		Betreut von\\ Prof. Dr.-Ing. Kane \\ Prof. Dr.-Ing. Thomas Schüning \\ Prof. Dr. rer. nat. Walter Neu

	\end{center}
	\normalsize
\end{titlepage}

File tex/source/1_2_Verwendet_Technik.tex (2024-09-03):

\chapter{Stand der Technik}

\section{Konzept}
Der Pod wird von einem BLDC-Motor angetrieben, wobei die elektrische Energie in einem Lithium-Ionen-Akku gespeichert wird. Der Motor wird durch einen Sinuswellen-Generator gesteuert. Mit dem Speedgoat-System werden die Eingangssignale des Sinuswellen-Generators sowie andere Aktoren gesteuert.

\section{Antrieb – Golden Motor}
\label{Golden_Motor}

\myboxy{
	\begin{itemize}
		\item Bilder neu machen aus dem Schaltplan.
		\item Vector Controller, Funktionsweise nur kurz erklären und mehr auf die Anschlüsse eingehen.
		\item PIN-Mapping als Tabelle erstellen, für den Motor und den Vector Controller.
	\end{itemize}
}{To-do}{\textwidth}

Golden Motor ist ein Anbieter von Elektromotoren und elektrischen Antriebssystemen. Das Unternehmen bietet eine breite Palette von Produkten an, darunter:
Motoren und Komplettsysteme für Elektrofahrräder, Industrielle BLDC-Motoren, Elektrische Antriebe für Boote.

\subsection{BLDC Motor}
\label{BLDC_Motor}

Ein BLDC-Motor (Brushless DC Motor) unterscheidet sich grundlegend von einem herkömmlichen Gleichstrommotor. Während bei einem traditionellen DC-Motor die Polumschaltung (Kommutierung) mechanisch über Kohlebürsten erfolgt, übernimmt beim BLDC-Motor eine elektronische Steuerung diese Aufgabe. Dadurch entfällt die Notwendigkeit von Kohlebürsten, was den Motor effizienter und langlebiger macht\cite{mathworks:bldc_motor}.

\begin{figure}[ht]
	\begin{center}
		
		\caption{Golden Motor – 10 KW BLDC Motor Liquid Cooled}
		\label{img_2_2:antrieb_motor:1}
	\end{center}
\end{figure}

Die Anschlüsse des BLDC-Motors sind in Abbildung \ref{img_2_2:circ_bldc:1} dargestellt. Der Motor verfügt über zwei Ausgänge, die jeweils mit drei Hall-Sensoren ausgestattet sind, sowie über einen Temperatursensor. Zusätzlich werden über das Kabel ein GND und eine +5V-Versorgung benötigt. Die Spulen des Motors werden über drei Phasen angeschlossen: U, V und W.

\begin{figure}[ht]
	\begin{center}
		
		\caption{Golden Motor – Zeichnung: BLDC Motor}
		\label{img_2_2:circ_bldc:1}
	\end{center}
\end{figure}

\subsection{Vector Controller}
Der Vector Controller verwendet die Motorsteuerungstechnologie feldorientierte Regelung (Field-Oriented Control - FOC), dass bedeutet das der Controller mittels den Hallsensoren, einem Rückgekoppelten Regelkreis bildet und somit die Lage des Polrades ermittelt.

\cite{schroeder:elektische_antriebe}

Sie bietet eine effiziente Steuerung von BLDC-Motoren in Anwendungen mit variabler Drehzahl und schnell wechselnden Lasten und verbessert die Energieeffizienz von Asynchronmotoren, vor allem bei niedrigen Drehzahlen.

\begin{figure}[!ht]
	\begin{center}
		
		\caption{Golden Motor – VECTOR 500 Motor Controller}
		\label{img_2_2:antrieb_sine:1}
	\end{center}
\end{figure}

\begin{figure}[!ht]
	\begin{center}
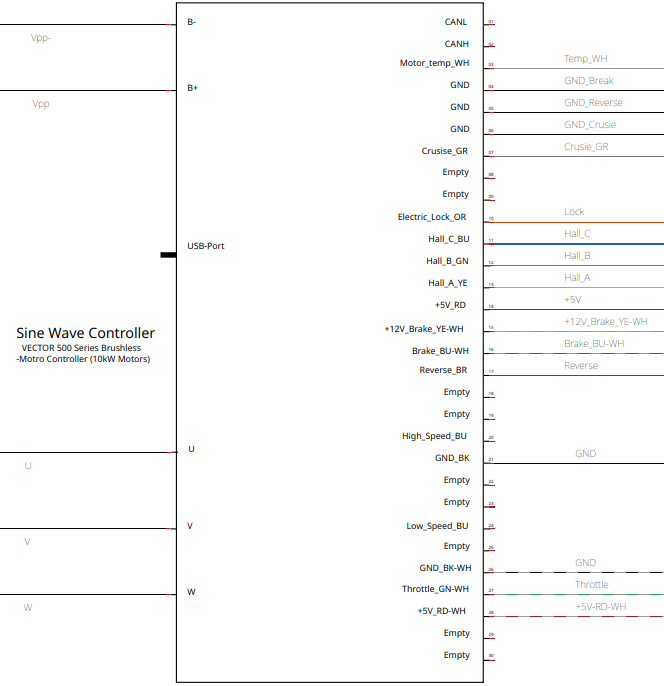
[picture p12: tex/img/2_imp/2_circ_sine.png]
		
		\caption{Golden Motor – Zeichnung: Vector Controller}
		\label{img_2_2:circ_sine:1}
	\end{center}
\end{figure}

\section{Steuerung – Speedgoat}

\myboxy{
	\begin{itemize}
		\item PIN-Mapping \ref{speedgoat:IO397B} überprüfen
		\item I/O Module 691 zuende Erklären.
	\end{itemize}
}{To-do}{\textwidth}

Speedgoat ist ein Unternehmen, das sich auf hochmoderne Echtzeitsysteme spezialisiert hat. Diese Systeme werden vor allem in der Entwicklung und dem Testen von komplexen Steuerungs- und Regelungssystemen eingesetzt.

\begin{figure}[!ht]
	\begin{center}
		
		\caption{Speedgoat – Baseline Real-Time Target Machine}
		\label{img_2_2:steuerung_goat:1}
	\end{center}
\end{figure}

Speedgoat-Systeme arbeiten nahtlos mit Simulink zusammen, einer Software von MathWorks, die häufig für die Modellierung und Simulation von dynamischen Systemen eingesetzt wird.
Speedgoat bietet eine breite Palette von I/O-Modulen an, die es ermöglichen, verschiedene Sensoren und Aktuatoren an die Systeme anzuschließen. Dies macht die Systeme sehr flexibel und anpassungsfähig.
Echtzeitsysteme von Speedgoat sind Computer, die in der Lage sind, Aufgaben innerhalb festgelegter Zeitintervalle auszuführen. Diese Systeme sind entscheidend für Anwendungen, bei denen die zeitliche Genauigkeit von großer Bedeutung ist, wie beispielsweise bei der Steuerung von Motoren, der Regelung von Prozessen oder der Simulation von physikalischen Systemen.

\subsection{Verbaute Module}

Für das Projekt wird die Baseline Real-Time Target Machine verwendet. Die über die Module IO397 und IO691 verfügt.\\

\begin{figure}[!ht]
	\begin{center}
		
		\caption{Speedgoat – I/O Module 397 \cite{speedgoat:IO397}}
		\label{img_2_2:goat:IO397}
	\end{center}
\end{figure}

Das IO397 I/O-Modul ist ein mPCIe-kompatibles, in Simulink programmierbares FPGA-Modul mit 50k Logikzellen, 4 ADC-Eingangs- und 4 DAC-Ausgangskanälen, sowie 14 ESD-geschützten TTL-I/O-Leitungen. Es unterstützt eine 16-Bit-Auflösung, softwareseitig auswählbare Spannungen und ist ideal für geschlossene Regelkreise und Hardware-in-the-Loop (HIL)-Simulationen mit MATLAB und Simulink \cite{speedgoat:IO397}.

\begin{figure}[ht]
	\begin{center}
		
		\caption{Speedgoat – I/O Module 691 \cite{speedgoat:IO691}}
		\label{img_2_2:goat:IO691}
	\end{center}
\end{figure}

Das IO691 I/O-Modul bietet eine intelligente CAN-Schnittstelle mit zwei Kanälen, die sowohl flexible Datenrate CAN (CAN FD) als auch High-Speed CAN (CAN HS) unterstützen. Es ist kompatibel mit CAN 2.0A/B-Netzwerken und unterstützt SAE J1939 sowie ASAM XCP für Bypassing. Alle Signale sind über 9-polige D-Sub-Front-CAN-Anschlüsse zugänglich. Das Modul ist ideal für geschlossene Regelkreise, Hardware-in-the-Loop-Simulationen und Restbussimulationen mit MATLAB und Simulink \cite{speedgoat:IO691}.

\subsection{Pin Mapping der Module}
Das Modul IO397-50k kann über ein Sensor-Aktor-Kabel von Phoenix Contact extern angeschlossen werden, wie in Abbildung \ref{img_2_2:steuerung_goat:2} dargestellt.
Zusätzlich wird das Modul IO691 mittels eines 9-Pin D-Sub-Steckers (männlich) angeschlossen.

\begin{figure}[ht]
	\begin{center}
		
		\caption{Speedgoat – Ansicht der Modulanschlüsse}
		\label{img_2_2:steuerung_goat:2}
	\end{center}
\end{figure}

%\begin{figure}[ht]
%	\begin{center}
%		\includegraphics[width=1\textwidth]{img/2_steuerung/goat_3.png}
%		\caption{Speedgoat – Ansicht der Kommunikationsschnittstellen}
%		\label{img_2_2:steuerung_goat:3}
%	\end{center}
%\end{figure}

\subsubsection{Pin Mapping – IO397-50k}

Terminal Board A ist für die Verarbeitung analoger Signale ausgelegt, sowohl für Eingänge als auch für Ausgänge. Die Tabelle \ref{speedgoat:IO397A} zeigt das Pin Mapping von Terminal Board A. Dieses Board enthält Anschlüsse für insgesamt vier analoge Eingänge (Pins 1a bis 8a) und vier analoge Ausgänge (Pins 9a bis 12a). Die analogen Eingänge sind für die Messung von Spannungen zuständig, wobei die positiven und negativen Leitungen (jeweils "+" und "-") getrennt geführt werden, um eine differenzielle Signalverarbeitung zu ermöglichen. Die Ausgänge sind digitale-zu-analoge-Wandler (DAC), die analoge Signale für den Antrieb von Geräten bereitstellen. Zusätzlich sind mehrere Ground- und Spannungsanschlüsse vorhanden, um eine stabile Stromversorgung zu gewährleisten.
\begin{table}[ht]
	\centering
	\caption{IO397-50k Pin   – Terminal Board A: analog I/O \cite{speedgoat:IO397}}
	\label{speedgoat:IO397A}
	\begin{tabular}{lcl}
		\hline
		\textbf{Pin}             & \textbf{Funktionalität} & \textbf{Type} \\ \hline
		\multicolumn{1}{l|}{1a}  & Analog input 01 (+)     & ADC           \\
		\multicolumn{1}{l|}{2a}  & Analog input 01 (-)     & ADC           \\
		\multicolumn{1}{l|}{3a}  & Analog input 02 (+)     & ADC           \\
		\multicolumn{1}{l|}{4a}  & Analog input 02 (-)     & ADC           \\
		\multicolumn{1}{l|}{5a}  & Analog input 03 (+)     & ADC           \\
		\multicolumn{1}{l|}{6a}  & Analog input 03 (-)     & ADC           \\
		\multicolumn{1}{l|}{7a}  & Analog input 04 (+)     & ADC           \\
		\multicolumn{1}{l|}{8a}  & Analog input 04 (-)     & ADC           \\ \hline
		\multicolumn{1}{l|}{9a}  & Analog output 01        & DAC           \\
		\multicolumn{1}{l|}{10a} & Analog output 02        & DAC           \\
		\multicolumn{1}{l|}{11a} & Analog output 03        & DAC           \\
		\multicolumn{1}{l|}{12a} & Analog output 04        & DAC           \\ \hline
		\multicolumn{1}{l|}{13a} & Ground                  &               \\
		\multicolumn{1}{l|}{14a} & Ground                  &               \\
		\multicolumn{1}{l|}{15a} & 0V                      &               \\
		\multicolumn{1}{l|}{16a} & 5V                      &               \\
		\multicolumn{1}{l|}{17a} & Ground                  &               \\
		\multicolumn{1}{l|}{SH}  & Shielding of M12 cable  &               \\ \hline
	\end{tabular}
\end{table}

Terminal Board B hingegen bietet eine flexible Konfiguration für digitale Ein- und Ausgänge. Die Tabelle \ref{speedgoat:IO397B} zeigt das Pin Mapping von Terminal Board B. Die Pins 3b bis 16b sind für konfigurierbare I/O-Funktionalitäten ausgelegt und nutzen TTL-Signale (Transistor-Transistor-Logik), was sie besonders für schnelle digitale Schaltvorgänge geeignet macht. Dieses Board ermöglicht es, die Anschlüsse flexibel zu nutzen, je nach den Anforderungen der Applikation. Auch hier gibt es mehrere Spannungs- und Ground-Anschlüsse, sowie eine Abschirmung (Shielding) für das M12-Kabel, um elektromagnetische Störungen zu minimieren.

\begin{table}[ht]
	\centering
	\caption{IO397-50k Pin Mapping – Terminal Board B: analog I/O \cite{speedgoat:IO397}}
	\label{speedgoat:IO397B}
	\begin{tabular}{lcl}
		\hline
		\textbf{Pin}             & \textbf{Funktionalität}        & \textbf{Type} \\ \hline
		\multicolumn{1}{l|}{1b}  & 0 V                            &               \\
		\multicolumn{1}{l|}{2b}  & 5 V                            &               \\\hline
		\multicolumn{1}{l|}{3b}  & Configurable I/O functionality & TTL           \\
		\multicolumn{1}{l|}{4b}  & Configurable I/O functionality & TTL           \\
		\multicolumn{1}{l|}{5b}  & Configurable I/O functionality & TTL           \\
		\multicolumn{1}{l|}{6b}  & Configurable I/O functionality & TTL           \\
		\multicolumn{1}{l|}{7b}  & Configurable I/O functionality & TTL           \\
		\multicolumn{1}{l|}{8b}  & Configurable I/O functionality & TTL           \\
		\multicolumn{1}{l|}{9b}  & Configurable I/O functionality & TTL           \\
		\multicolumn{1}{l|}{10b} & Configurable I/O functionality & TTL           \\
		\multicolumn{1}{l|}{11b} & Configurable I/O functionality & TTL           \\
		\multicolumn{1}{l|}{12b} & Configurable I/O functionality & TTL           \\
		\multicolumn{1}{l|}{13b} & Configurable I/O functionality & TTL           \\
		\multicolumn{1}{l|}{14b} & Configurable I/O functionality & TTL           \\
		\multicolumn{1}{l|}{15b} & Configurable I/O functionality & TTL           \\
		\multicolumn{1}{l|}{16b} & Configurable I/O functionality & TTL           \\\hline
		\multicolumn{1}{l|}{17b} & Ground                         &               \\
		\multicolumn{1}{l|}{SH}  & Shielding of M12 cable         &               \\ \hline
	\end{tabular}
\end{table}

\subsubsection{Pin Mapping –  IO691}

\begin{table}[ht]
	\centering
	\caption{IO691 Pin Mapping}
	\label{speedgoat:IO691}
	\begin{tabular}{ll}
		\hline
		\textbf{Pin}           & \textbf{DB9 Connector A/B, Signal} \\ \hline
		\multicolumn{1}{l|}{1} & -                                  \\
		\multicolumn{1}{l|}{2} & CAN-low                            \\
		\multicolumn{1}{l|}{3} & GND                                \\
		\multicolumn{1}{l|}{4} & -                                  \\
		\multicolumn{1}{l|}{5} & -                                  \\
		\multicolumn{1}{l|}{6} & GND                                \\
		\multicolumn{1}{l|}{7} & CAN-high                           \\
		\multicolumn{1}{l|}{8} & -                                  \\
		\multicolumn{1}{l|}{9} & -                                  \\ \hline
	\end{tabular}
\end{table}

\section{Abstandsmessung}
\begin{figure}[ht]
	\begin{center}
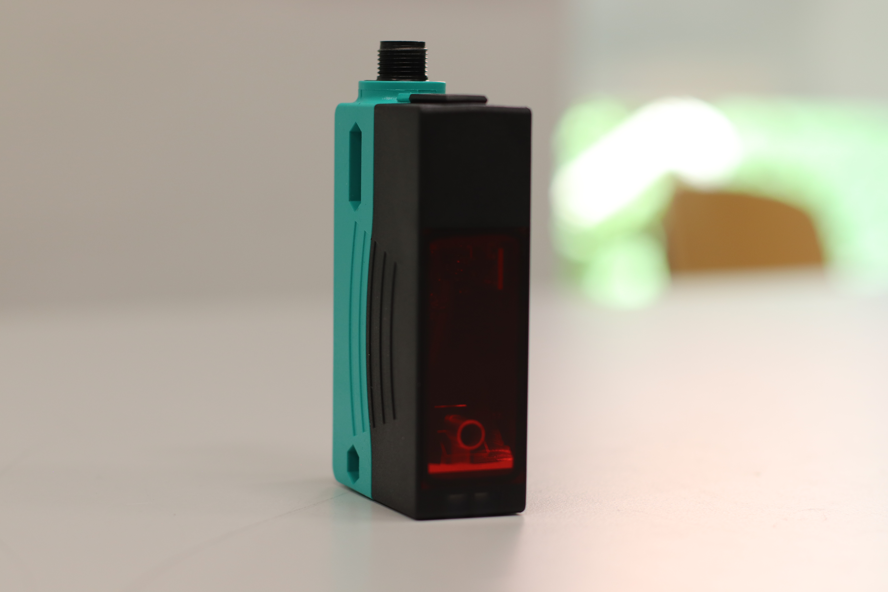
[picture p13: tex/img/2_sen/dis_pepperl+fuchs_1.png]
		
		\caption{Pepperl+Fuchs – Distanzsensor}
		\label{img_2_2:sen_dis:1}
	\end{center}
\end{figure}

\section{Speicher}

\begin{figure}[!ht]
	\begin{center}
		
		\caption{DeepCPower – Lithium Batterie 50Ah | 51,2V | 2560Wh}
		\label{img_2_2:speicher_1:1}
	\end{center}
\end{figure}

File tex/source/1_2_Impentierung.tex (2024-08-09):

\chapter{Impentierung}

\section{Konzepet}
Der Pod wird von einem BLDC-Motor angetrieben, wobei die elektrische Energie in einem Lithium-Ionen-Akku gespeichert wird. Der Motor wird durch einen Sinuswellen-Generator gesteuert. Mit dem Speedgoat-System werden die Eingangssignale des Sinuswellen-Generators sowie andere Aktoren gesteuert.

\section{Golden Motor}
\label{Golden_Motor}
Golden Motor ist ein Anbieter von Elektromotoren und elektrischen Antriebssystemen. Das Unternehmen bietet eine breite Palette von Produkten an, darunter:
Motoren und Komplettsysteme für Elektrofahrräder, Industrielle BLDC-Motoren, Elektrische Antriebe für Boote.

\subsection{BLDC Motor}
\label{BLDC_Motor}
Ein BLCD Motor wird mit Gleichspannung angetrieben, wobei eine Leistungssteuerung (Sinuswellen-Generator) die Gleichspannung in ein nutzbares Drehstom umwandelt, dies verhalten wird in Abschnitt \ref{Sinuswellen-Generator} näher erläutert.\\

Da der Motor keine Schleifkontakte (Kohlebürsten) hat, entsteht kein abrieb. Die Kommutierung, also die Umschaltung der Stromrichtung in den Spulen, erfolgt elektronisch.

Im Rotor (dem rotierenden Teil) befinden sich Permanentmagnete. Im Stator (dem feststehenden Teil) sind Spulen angeordnet. Durch gezieltes Ansteuern der Spulen wird ein magnetisches Drehfeld erzeugt, das den Rotor mit den Permanentmagneten mitnimmt.

\begin{figure}[!ht]
	\begin{center}
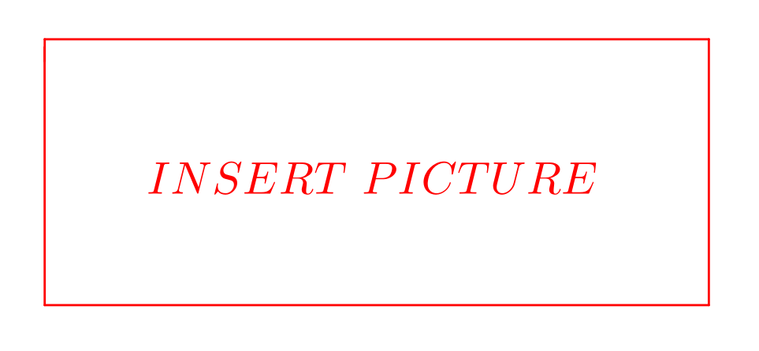
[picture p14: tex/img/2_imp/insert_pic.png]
		
		\caption{10 KW BLDC Motor Liquid Cooled}
		\label{img_2_2:motor}
	\end{center}
\end{figure}

\subsection{Sinuswellen-Generator}
\label{Sinuswellen-Generator}

%Dafür muss der Abstand ermittelt werden, dies wird mit einem Abstandslaser gemacht.

%Die Steuerung wird als Automaten umgesetzt. Dabei werden unterschiedliche Zustände durchlaufen, wie Idel, Drive, Distance und Stop.

\section{Verdrahtung}

\section{Schaltpaln}

\section{Simulink}

\

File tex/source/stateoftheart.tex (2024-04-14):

\chapter{Grundlagen und Stand der Technik}
\section{Aufbau vom 600 V Pod}

Der Aufbau des Hyperloop-Pods umfasst eine Batterie mit einer Boardspannung von 600 V sowie einen Wechselrichter, der die Spannung von Gleichstrom zu Wechselstrom umwandelt. Die Kontrolleinheit besteht aus einem Speedgoat, der Signale in Echtzeit erfasst und ausgibt. Die Drehzahl wird mithilfe eines Odometers gemessen.

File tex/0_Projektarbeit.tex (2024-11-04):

\documentclass[oneside,a4paper,11pt]{book} 
\setcounter{secnumdepth}{4}
\setcounter{tocdepth}{4}   
\usepackage{fancyhdr}
\setlength{\headheight}{15pt}
\usepackage[pdftex,
pdfauthor={Name, Vorname},
pdftitle={Überschrift},
pdfsubject={Projektarbeit},
pdfkeywords={Unterschrift}
]{hyperref}
\usepackage[ngerman]{babel}
\usepackage[T1]{fontenc}
\usepackage[utf8]{inputenc}
\usepackage[dvips]{graphicx}
\usepackage{calc}
\usepackage{makeidx}
\usepackage[hang,small,scriptsize,bf]{caption}
\usepackage{hsel-thesis2020}
\usepackage{amssymb}
\usepackage{amsmath}
\usepackage{subcaption}
\usepackage{hyperref}
\usepackage{multirow}
\usepackage{circuitikz}
\usepackage{seqsplit}
\usepackage{csquotes}
\usepackage{makecell}
\usepackage{animate}
\usepackage{eso-pic}
\usepackage{newfloat}
\usepackage{pdfpages}
\usepackage{tikz}
\usepackage{listings}
\usepackage{fixltx2e}
\usepackage{flowchart}

\usepackage{silence}
\WarningFilter*{latex}{Text page \thepage\space contains only floats}

\usepackage[normalem]{ulem}
\usepackage[
  style=numeric,
  sorting=none,
  backend=biber
  ]{biblatex}
\addbibresource{Literaturverzeichnis.bib}
\usetikzlibrary{positioning}

\usepackage{colortbl}
\usepackage[table]{xcolor}

\newcommand{\myboxy}[3]{
	\begin{tikzpicture}[
			every node/.style={rectangle,rounded corners,draw=black, top color=white,very thick, inner sep=0.3em, minimum size=1em} ]
		\node[text width=#3](main) at (0,0 ){\vspace{3pt}  #1};
		\node[above =-2mm of main.north west, anchor=south west] (title) {#2};
	\end{tikzpicture} }

\newcommand{\textbfit}[1]{\textbf{\textit{#1}}}

\pdfcompresslevel=5 

\DeclareFloatingEnvironment[
	listname  = {Diagrammverzeichnis}, % Listenüberschrift
	name      = Diagramm,              % Name in Beschriftungen
]{scheme}

\DeclareFloatingEnvironment[
	listname  = {Oszillogrammverzeichnis}, % Listenüberschrift
	name      = Oszillogramm,              % Name in Beschriftungen
]{oszillo}

%%%%%%%%%%%%%%%%%%%%%%%%%%%%%%%%%%%%%%%%%%%%%%%%%%%%%%%%%%%%%%%%%%%%%%%%%%%%%%%%%%%%
%%%%%%%%%%%%%%%%%%%%%%%%%%%%%%%%%%%%%%%%%%%%%%%%%%%%%%%%%%%%%%%%%%%%%%%%%%%%%%%%%%%%
%%%%%%%%%%%%%%%%%%%%%%%%%%%%%%%%%%%%%%%%%%%%%%%%%%%%%%%%%%%%%%%%%%%%%%%%%%%%%%%%%%%%
%%%%%%%%%%%%%%%%%%%%%%%%%%%%%%%%%%%%%%%%%%%%%%%%%%%%%%%%%%%%%%%%%%%%%%%%%%%%%%%%%%%%
%%%%%%%%%%%%%%%%%%%%%%%%%%%%%%%%%%%%%%%%%%%%%%%%%%%%%%%%%%%%%%%%%%%%%%%%%%%%%%%%%%%%
%%%%%%%%%%%%%%%%%%%%%%%%%%%%%%%%%%%%%%%%%%%%%%%%%%%%%%%%%%%%%%%%%%%%%%%%%%%%%%%%%%%%

\begin{document}
\allsectionsfont{\sffamily}

\AddToShipoutPicture{\BackgroundWave}
\pagenumbering{Roman}

\include{source/0_0_Titelseite}
\linespread{1.2}
\noitemsep
\include{source/0_1_RechtlicheErklärung}
\include{source/0_2_Verzeichnis}

\cleardoublepage
\pagenumbering{arabic}
\ClearShipoutPicture

\include{source/1_0_Einleitung}
\include{source/einennoch}
\include{source/1_2_Konzept}
\include{source/einennoch}
\include{source/1_3_Verwendet_Technik}
\include{source/einennoch}
\include{source/1_4_Implementierung}
\include{source/einennoch}
\include{source/1_5_Konklusion}
\include{source/einennoch}
\include{source/Literaturverzeichnis}
\printbibliography
\appendix
\include{source/einennoch}
\include{source/2_0_Anhang}

\end{document}

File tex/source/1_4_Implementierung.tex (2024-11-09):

\chapter{Implementierung}
\label{chapter:Implementierung}

\section{Schaltplan}
\label{section:Schaltplan}
Zu Beginn der Erstellung des Schaltplans sollten die Funktions- und Ortskennzeichen sowie die Beschriftung der Bauteile und Leitungen festgelegt werden. Bei der Verdrahtung ist es erforderlich, die Aderfarben den entsprechenden Spannungspotenzialen zuzuordnen.

\subsection{Betriebsmittelbezeichnung}
\label{Schaltplan:BMK}

Ein Betriebsmittel besteht aus verschiedenen Kennzeichen: dem Funktionskennzeichen (=), dem Ortskennzeichen (+) und dem Betriebsmittelkennzeichen (-). Früher wurde das Funktionskennzeichen als „Anlage“ bezeichnet. In der neuen DIN EN IEC 81346-2 \cite{DIN_EN_IEC_81346-2} wurde diese Bezeichnung jedoch auf „Funktion“ geändert.

\subsubsection{Funktionskennzeichen}
Das Funktionskennzeichen beschreibt eine bestimmte Funktion im Schaltplan, wie beispielsweise die Spannungsversorgung oder die Steuerung (siehe Tabelle \ref{BMK:tab:funktionskennzeichen}).

\pagebreak[1]
\begin{table}[!ht]
	\centering
	\caption{Schaltplan – Funktionskennzeichen (=)}
	\label{BMK:tab:funktionskennzeichen}
	\begin{tabular}{ll}
		\hline
		\textbf{Abkürzung}      & \textbf{Bezeichnung} \\ \hline
		\multicolumn{1}{l|}{SV} & Spannungsversorung   \\
		\multicolumn{1}{l|}{ST} & Steuerung            \\
		\multicolumn{1}{l|}{ES} & Eingänge Steuerung   \\
		\multicolumn{1}{l|}{AS} & Ausgänge Steuerung   \\
		\multicolumn{1}{l|}{KL} & Klemmenleisten       \\
		\multicolumn{1}{l|}{KO} & Kommunikation        \\
		\multicolumn{1}{l|}{AT} & Antrieb              \\
		\multicolumn{1}{l|}{NA} & Not-Aus              \\ \hline
	\end{tabular}
\end{table}
\pagebreak[1]

\subsubsection{Ortskennzeichen}
Das Ortskennzeichen gibt an, an welchem Ort ein Bauteil installiert ist. Beispielsweise gibt es im Fahrzeug eine Steuereinheit und eine Batterieeinheit. Im Schaltplan wird dadurch deutlich, welche Verbindungen zwischen verschiedenen Orten bestehen. Das Ortskennzeichen erleichtert zudem die Wartung und Installation des Systems.

\pagebreak[1]
\begin{table}[!ht]
	\centering
	\caption{Schaltplan – Ortskennzeichen (+)}
	\label{bmk:tab:ortskennzeichen}
	\begin{tabular}{ll}
		\hline
		\textbf{Abkürzung}       & \textbf{Bezeichnung} \\ \hline
		\multicolumn{1}{l|}{POD} & Fahrzeug             \\
		\multicolumn{1}{l|}{BE}  & Batterieeinheit      \\
		\multicolumn{1}{l|}{SE}  & Steuereinheit        \\
		\multicolumn{1}{l|}{AE}  & Antriebseinheit      \\ \hline
	\end{tabular}
\end{table}
\pagebreak[1]

\subsubsection{Betriebsmittelkennzeichen}
Das Betriebsmittelkennzeichen bezeichnet das spezifische Bauteil. Die genaue Zuordnung der Bezeichnungen ist in der DIN EN IEC 81346-2 geregelt. Die für das Projekt relevanten Betriebsmittelkennzeichen sind in Tabelle \ref{bmk:tab:betriebsmittelkennzeichen} aufgeführt.

\pagebreak[1]
\begin{table}[!ht]
	\centering
	\caption{Schaltplan – Betriebsmittelkennzeichen (-) \cite{DIN_EN_IEC_81346-2}}
	\label{bmk:tab:betriebsmittelkennzeichen}
	\begin{tabular}{|l|lll|}
		\hline
		\textbf{Abkürzung}           & \textbf{Klassenname}                               & \multicolumn{1}{l|}{\makecell[l]{\textbf{Allgemeine} \\ \textbf{Bedeutung}}} \\ \hline
		\multicolumn{1}{|l|}{BG}     & \makecell[l]{\makecell[l]{Objekt zur Erkennung von                                                        \\
		physikalischen Dimensionen}} & \multicolumn{1}{l|}{Sensor}                                                                               \\ \hline
		\multicolumn{1}{|l|}{FC}     & \makecell[l]{Überstromschutzobjekt}                & \multicolumn{1}{l|}{Sicherung}                       \\ \hline
		\multicolumn{1}{|l|}{GB}     & \makecell[l]{Erzeugungsobjekt für elektrische                                                             \\Energie durch chemische Energie} & \multicolumn{1}{l|}{Batterie} \\ \hline
		\multicolumn{1}{|l|}{KE}     & \makecell[l]{Elektrische Signale                                                                          \\verarbeitendes Objekt}   & \multicolumn{1}{l|}{Steuerung} \\ \hline
		\multicolumn{1}{|l|}{MA}     & \makecell[l]{Elektromagnetisches                                                                          \\Rotationsantriebsobjekt} & \multicolumn{1}{l|}{Motor} \\ \hline
		\multicolumn{1}{|l|}{QA}     & \makecell[l]{Stromsteuerungsobjekt}                & \multicolumn{1}{l|}{Relais}                          \\ \hline
		\multicolumn{1}{|l|}{RL}     & \makecell[l]{Bewegungsbegrenzungsobjekt}           & \multicolumn{1}{l|}{Bremse}                          \\ \hline
		\multicolumn{1}{|l|}{SF}     & \makecell[l]{Fingerinteraktionsobjekt}             & \multicolumn{1}{l|}{Schalter}                        \\ \hline
		\multicolumn{1}{|l|}{TB}     & \makecell[l]{Stromkonvertierungsobjekt}            & \multicolumn{1}{l|}{Transformator}                   \\ \hline
		\multicolumn{1}{|l|}{WD}     & \makecell[l]{Niederspannungsenergie Leitobjekt}    & \multicolumn{1}{l|}{Leitung/Kabel}                   \\ \hline
		\multicolumn{1}{|l|}{XD}     & \makecell[l]{Niederspannungs-Verbindungsobjekt}    & \multicolumn{1}{l|}{\makecell[l]{Klemme, Stecker     \\ oder Buchse}} \\ \hline
	\end{tabular}
\end{table}
\pagebreak[1]

Bei einer vollständigen Betriebsmittelbezeichnung sieht das Kennzeichen des Betriebsmittels folgendermaßen aus:

\begin{center} =ES2+SE1-10QA1 \end{center}

Die Betriebsmittelbezeichnung =ES2+SE1-10QA4 besagt, dass es sich um die Eingänge der Steuerung (=ES) handelt und es gibt zwei Funktionen in dem Schaltplan. Der Ort ist in der Steuereinheit (+SE) verortet, und das Betriebsmittel selbst ist ein Relais, welche auf der Seite 10 des Schaltplans zu finden ist.

Das Kennzeichen umfasst sowohl das Funktions- als auch das Ortskennzeichen, die jeweils mit einer fortlaufenden Nummer versehen werden. Das Betriebsmittelkennzeichen enthält zwei Nummerierungen: Die erste gibt an, auf welcher Seite des Schaltplans sich das Betriebsmittel befindet, während die zweite die fortlaufende Nummerierung des Bauteils darstellt.\\
Im Schaltplan wird das Betriebsmittel lediglich durch das Betriebsmittelkennzeichen (-) dargestellt, während das Funktions- und Ortskennzeichen im Zeichnungskopf angegeben ist.

\newpage

\subsection{Verdrahtung Konventionen}
\label{section:Verdrahtung_Konventionen}
Für die Verdrahtung müssen den Spannungspotenzialen verschiedene Farben zugewiesen werden. Diese Zuordnungen sind in Tabelle \ref{Verdrahtung_Konventionen:tab:Zuordnung} aufgeführt.
\pagebreak[1]
\begin{table}[!ht]
	\centering
	\caption{Verdrahtung Konvention – Aderfarben}
	\label{Verdrahtung_Konventionen:tab:Zuordnung}
	\begin{tabular}{lccl}
		\hline
		\textbf{Farbe}                & \textbf{U in V} & \textbf{A in mm$^2$} & \textbf{Funktion}       \\ \hline
		\multicolumn{1}{l|}{Rot}      & $24$            & 1                    & Steuerspannung          \\
		\multicolumn{1}{l|}{Blau}     & $x$             & 1                    &                         \\
		\multicolumn{1}{l|}{Schwarz}  & $GND$           & 1                    & Masse Steuerspannung    \\
		\multicolumn{1}{l|}{Schwarz}  & $< 48$          & 50                   & Batteriespannung (Last) \\
		\multicolumn{1}{l|}{Viollett} & $5$             & 1                    & Steuerung               \\ \hline
	\end{tabular}
\end{table}
\pagebreak[4]

\newpage

%%%%%%%%%%%%%%%%%%%%%%%%%%%%%%%%%%%%%%%%%%%%%%%%%%%%%%%%%%%%%%%%%%%%%%%%%%%%%%%%%%%%
%%%%%%%%%%%%%%%%%%%%%%%%%%%%%%%%%%%%%%%%%%%%%%%%%%%%%%%%%%%%%%%%%%%%%%%%%%%%%%%%%%%%
%%%%%%%%%%%%%%%%%%%%%%%%%%%%%%%%%%%%%%%%%%%%%%%%%%%%%%%%%%%%%%%%%%%%%%%%%%%%%%%%%%%%
%%%%%%%%%%%%%%%%%%%%%%%%%%%%%%%%%%%%%%%%%%%%%%%%%%%%%%%%%%%%%%%%%%%%%%%%%%%%%%%%%%%%
%%%%%%%%%%%%%%%%%%%%%%%%%%%%%%%%%%%%%%%%%%%%%%%%%%%%%%%%%%%%%%%%%%%%%%%%%%%%%%%%%%%%
%%%%%%%%%%%%%%%%%%%%%%%%%%%%%%%%%%%%%%%%%%%%%%%%%%%%%%%%%%%%%%%%%%%%%%%%%%%%%%%%%%%%

\newpage
\section{Simulation mit Simulink}
\label{section:Simulation}

\subsection{Funktionsweise der Steuerung}
\label{Steuerung}

Die Steuerung des Fahrzeugs bietet die Möglichkeit, zwischen Automatik- und manuellem Betrieb zu wählen. Im manuellen Betrieb kann der Benutzer das Fahrzeug sowohl vorwärts als auch rückwärts bewegen, wobei zwei Geschwindigkeitsstufen – schnell und langsam – zur Verfügung stehen. Diese Funktion erlaubt dem Nutzer, das Fahrzeug innerhalb der Röhre individuell zu steuern und es hinein- und herauszufahren.\\
Im Automatikmodus beschleunigt das Fahrzeug auf eine einstellbare Geschwindigkeit und bremst automatisch ab, sobald eine bestimmte Distanz zum Enddeckel der Röhre erreicht ist. Schließlich hält es am Ende der Strecke an.\\

\subsubsection{Controlpanel}
\label{Steuerung:Controlpanel}
Über das Control Panel (siehe Abbildung \ref{Controlpanel:img:Controlpanel}) können alle Eingaben via Simulink gesteuert werden. Mit dem Wahlschalter kann, zwischen Automatik- und manuellem Betrieb gewechselt werden. Ist der manuelle Betrieb ausgewählt, kann mit dem Drehschalter (Manuell) zwischen Vorwärts, Rückwärts und Stopp geschaltet werden (siehe Tabelle \ref{Controlpanel:tab:Wahlschalter}, die Werte werden später für die Automatensteuerung benötigt).\\

\pagebreak[1]
\begin{table}[!ht]
	\centering
	\caption{Automat – Wahlschalter für den manuellen Betrieb}
	\label{Controlpanel:tab:Wahlschalter}
	\begin{tabular}{ccc}
		\hline
		\textbf{Schalterbezeichnung} & \textbf{Zustände} & \textbf{Wert} \\ \hline
		\multicolumn{1}{c|}{Rück+}   & Forwards fast     & 1             \\
		\multicolumn{1}{c|}{Rück}    & Forwards slow     & 2             \\
		\multicolumn{1}{c|}{STOP}    & Manual idle       & 3             \\
		\multicolumn{1}{c|}{Vor}     & Backwards slow    & 4             \\
		\multicolumn{1}{c|}{Vor+}    & Backwards fast    & 5             \\ \hline
	\end{tabular}
\end{table}
\pagebreak[3]
Im Automatikbetrieb kann die Geschwindigkeit über das Drehrad \frqq Geschwindigkeit Automatik\flqq\ voreingestellt oder während der Fahrt angepasst werden. Das Fahrzeug beginnt zu fahren, sobald der Druckknopf \frqq Start\flqq\ betätigt wird. Die Automatik kann über den Druckknopf \frqq Stop\flqq\ gestoppt werden.\\ Im Notfall kann sowohl im Automatik- als auch im manuellen Betrieb der Druckknopf \frqq Emergency stop\flqq\ betätigt werden. Das Fahrzeug führt eine Vollbremsung mit der Motor- und der mechanischen Bremse durch. Der Notfallmodus kann durch Drücken des \frqq Reset\flqq\ -Knopfs beendet werden.\\
Die Funktionsweise der manuellen Steuerung wird in Abschnitt \ref{Automatensteuerung:Automat_man} erklärt, und die der automatischen Steuerung in Abschnitt \ref{Automatensteuerung:Automat_auto}

\pagebreak[1]
\begin{figure}[!ht]
	\begin{center}
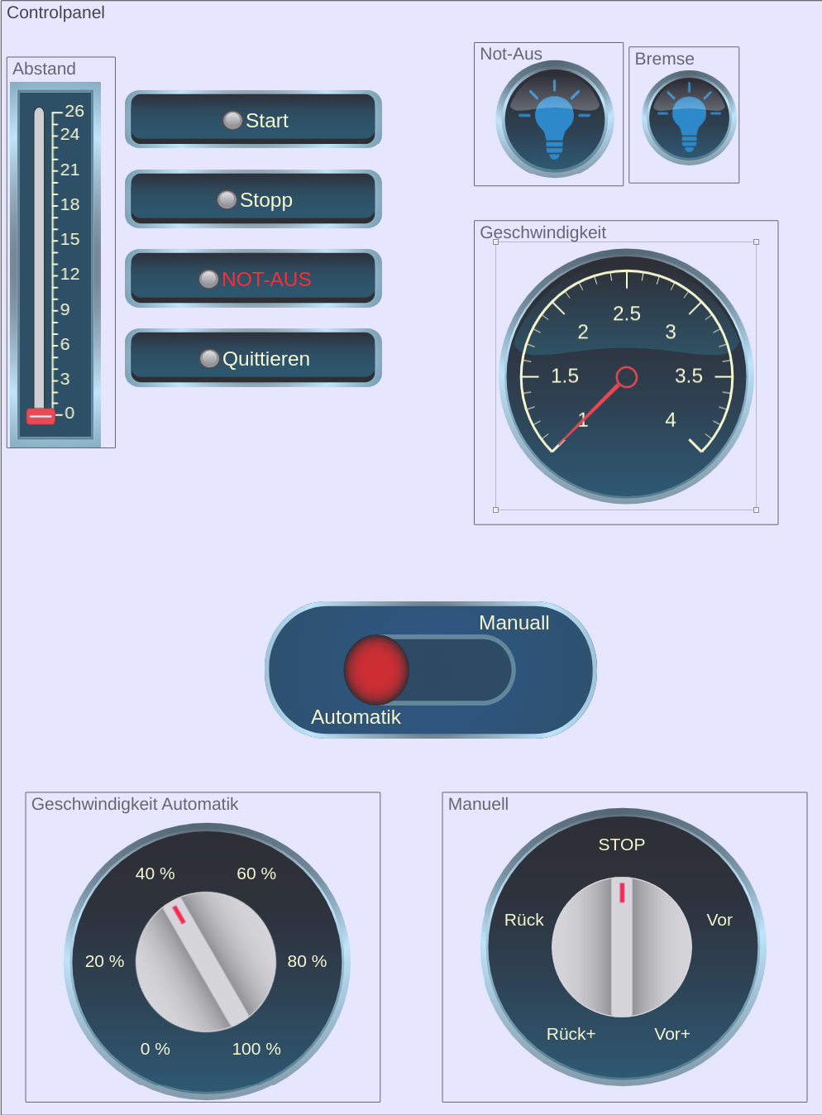
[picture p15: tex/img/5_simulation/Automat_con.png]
		
		\caption{Automat – Controlpanel}
		\label{Controlpanel:img:Controlpanel}
	\end{center}
\end{figure}
\pagebreak[4]

\subsection{Automatensteuerung}
\label{Automatensteuerung}
Die Automatensteuerung beschreibt die logische Steuerung eines Systems durch einen Automaten, wie etwa einen Moore- oder Mealy-Automaten, der auf Basis von Eingaben und aktuellen Zuständen Ausgaben steuert.\\
Das Fahrzeug wird mittels eines Moore-Automaten gesteuert, wobei die Ausgänge erst dann aktiviert werden, wenn sich das System im entsprechenden Zustand befindet.\\ \ \\
Der Automat startet im Zustand \frqq Idle\flqq\ siehe Abbildung \ref{Automat_man:tab:z_idle}, und die Abläufe für den automatischen oder manuellen Modus werden von \frqq Idle\flqq\ aus angesteuert. Im Zustand Idle werden die Ausgänge (siehe Tabelle \ref{Automat_man:tab:z_idle}) geschaltet.\\

\pagebreak[1]
\begin{figure}[!ht]
	\begin{center}
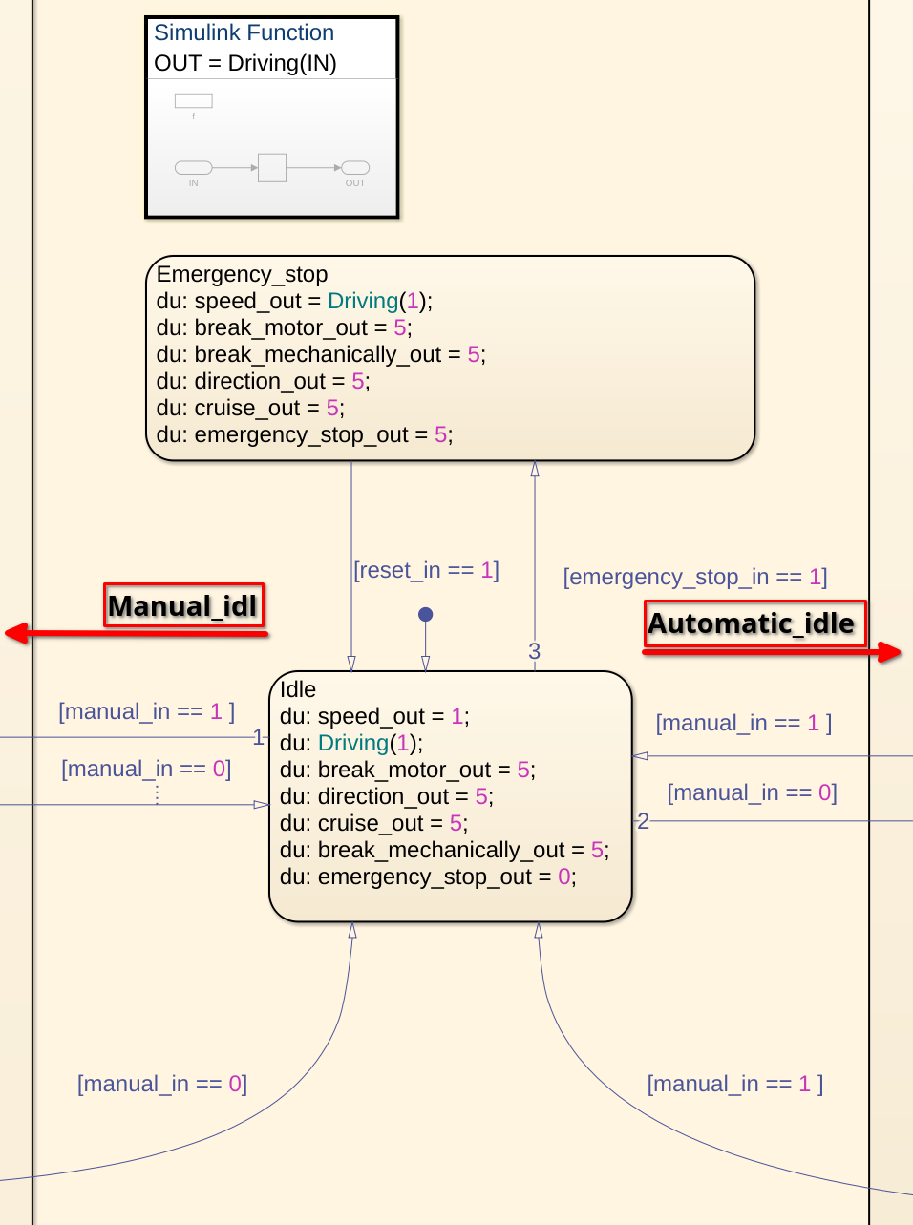
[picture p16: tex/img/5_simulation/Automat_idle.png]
		
		\caption{Automat – Start Zustand \frqq Idle\flqq}
		\label{Automat_man:img:start_idle}
	\end{center}
\end{figure}
\pagebreak[4]

\pagebreak[1]
\begin{table}[!ht]
	\centering
	\caption{Ausgänge – Idle}
	\label{Automat_man:tab:z_idle}
	\begin{tabular}{lll}
		\hline
		\textbf{Ausgänge}                           & \textbf{I/O Module}                 & \textbf{Wert} \\ \hline
		\multicolumn{1}{l|}{speed out}              & \multicolumn{1}{l|}{IO397-50k – A1} & 1             \\
		\multicolumn{1}{l|}{Driving(1)}             & \multicolumn{1}{l|}{}               & Reset         \\
		\multicolumn{1}{l|}{break motor out}        & \multicolumn{1}{l|}{IO397-50k – B3} & 5             \\
		\multicolumn{1}{l|}{direction out}          & \multicolumn{1}{l|}{IO397-50k – B4} & 5             \\
		\multicolumn{1}{l|}{cruise out}             & \multicolumn{1}{l|}{IO397-50k – B5} & 5             \\
		\multicolumn{1}{l|}{break mechanically out} & \multicolumn{1}{l|}{IO397-50k – B6} & 5             \\
		\multicolumn{1}{l|}{emergency stop out}     & \multicolumn{1}{l|}{IO397-50k – B7} & 0             \\ \hline
	\end{tabular}
\end{table}
\pagebreak[1]

Die Funktion \frqq Driving\flqq, siehe Abbildung \ref{Automat:img:fnc_Driving}, erhält einen Eingangswert, der durch einen \frqq Rate Limiter\flqq\ begrenzt und am Ausgang ausgegeben wird. Die Funktion speichert den letzten Wert, daher muss sie in den Zuständen, in denen das Fahrzeug angehalten wird, zurückgesetzt werden. Dies geschieht, indem die Funktion \frqq Driving\flqq\ den Wert \frqq 1\flqq\ erhält.\\

\pagebreak[1]
\begin{figure}[!ht]
	\begin{center}
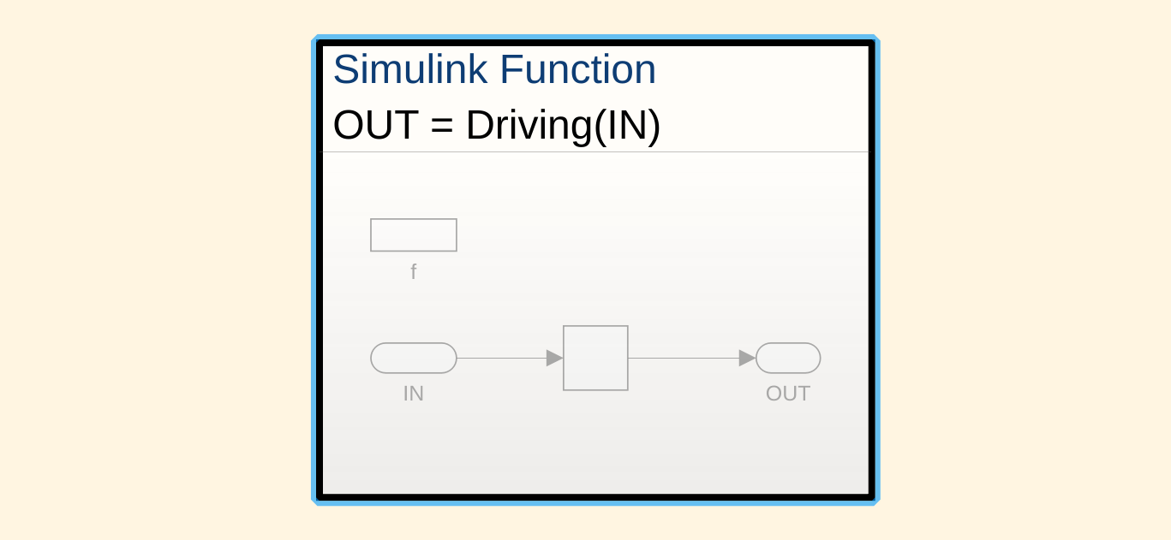
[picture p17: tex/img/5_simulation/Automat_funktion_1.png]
		
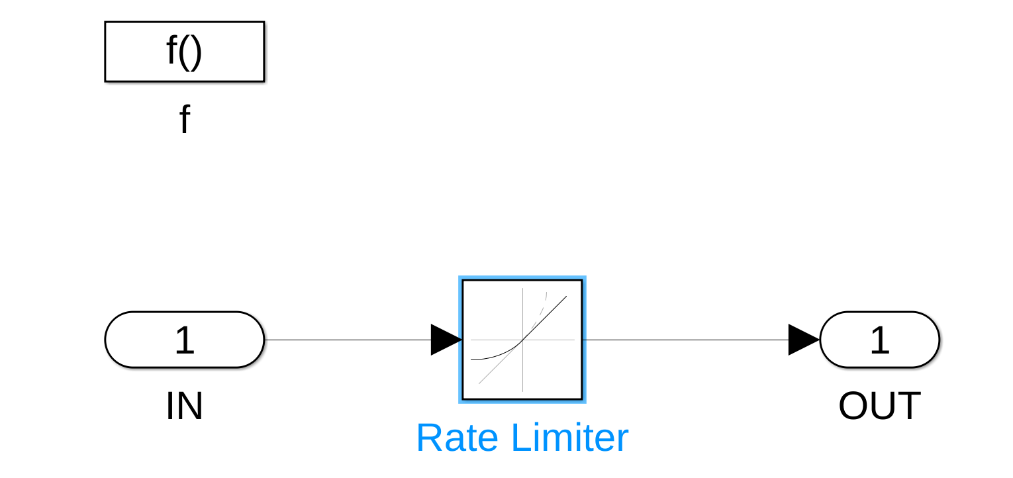
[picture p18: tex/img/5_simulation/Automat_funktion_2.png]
		
		\caption{Automat – Funktion Driving}
		\label{Automat:img:fnc_Driving}
	\end{center}
\end{figure}
\pagebreak[4]

Der Zustand \frqq Emergency stop\flqq\ kann von jedem Zustand aus durch den Eingang \frqq emergency stop in\flqq\ erreicht werden, welcher sowohl über das Controlpanel als auch extern über das IO397-50k – B11 ausgelöst werden kann. Der Zustand kann nur durch die Quittierung verlassen werden und führt dann in einen der Idle-Zustände zurück: \frqq Idle\flqq\ \frqq Manual idle\flqq\ oder \frqq Automatic idle\flqq. Im Zustand \frqq Emergency stop\flqq\ werden die Ausgänge gemäß Tabelle \ref{Automat_man:tab:z_Emergency_stop} geschaltet.

\pagebreak[1]
\begin{table}[!ht]
	\centering
	\caption{Ausgänge – Emergency stop}
	\label{Automat_man:tab:z_Emergency_stop}
	\begin{tabular}{lll}
		\hline
		\textbf{Ausgänge}                           & \makecell{\textbf{I/O Module}         \\ \textbf{IO397-50k}}                 & \textbf{Wert} \\ \hline
		\multicolumn{1}{l|}{speed out=Driving()}    & \multicolumn{1}{l|}{A1}       & Reset \\
		\multicolumn{1}{l|}{break motor out}        & \multicolumn{1}{l|}{}         & 5     \\
		\multicolumn{1}{l|}{direction out}          & \multicolumn{1}{l|}{B4}       & 5     \\
		\multicolumn{1}{l|}{cruise out}             & \multicolumn{1}{l|}{B5}       & 5     \\
		\multicolumn{1}{l|}{break mechanically out} & \multicolumn{1}{l|}{B6}       & 5     \\
		\multicolumn{1}{l|}{emergency stop out}     & \multicolumn{1}{l|}{B7}       & 5     \\ \hline
	\end{tabular}
\end{table}
\pagebreak[1]

\subsubsection{Automat für die manuelle Steuerung}
\label{Automatensteuerung:Automat_man}

Die manuelle Steuerung bietet dem Nutzer die Flexibilität, das Fahrzeug sowohl innerhalb als auch außerhalb der Röhre zu steuern.\\

Der Automat des manuellen Ablaufs, wie in Abbildung \ref{Automat_man:img:man_übersicht} dargestellt, ist in zwei Stateflows unterteilt: \frqq Forwards\flqq\ und \frqq Backwards\flqq . In Abbildung \ref{Automat_man:img:man_vorwärts} ist der \frqq Forwards\flqq\ -Stateflow zu sehen, der \frqq Backwards\flqq\ -Stateflow ist äquivalent, wobei sich lediglich der Ausgang \frqq Direction Out\flqq\ ändert. Daher wird nur der \frqq Forwards\flqq\ -Stateflow erklärt. Der Zustand \frqq Emerency stop 1\flqq\ ist der gleiche Zustand wie \frqq Emergency stop\flqq.
Die Ausgänge für die Zustände \frqq Forwards\flqq\ und \frqq Backwards\flqq\ sind in 2 Tabellen aufgeführt \ref{Automat_man:tab:z_V_langsam} und \ref{Automat_man:tab:z_V_schnell} aufgeführt, hierbei ist die erste Tabelle die Zustände \frqq slow\flqq\ und die zweite Tabelle für die Zustände \frqq fast\flqq.

\pagebreak[1]
\begin{figure}[!ht]
	\begin{center}
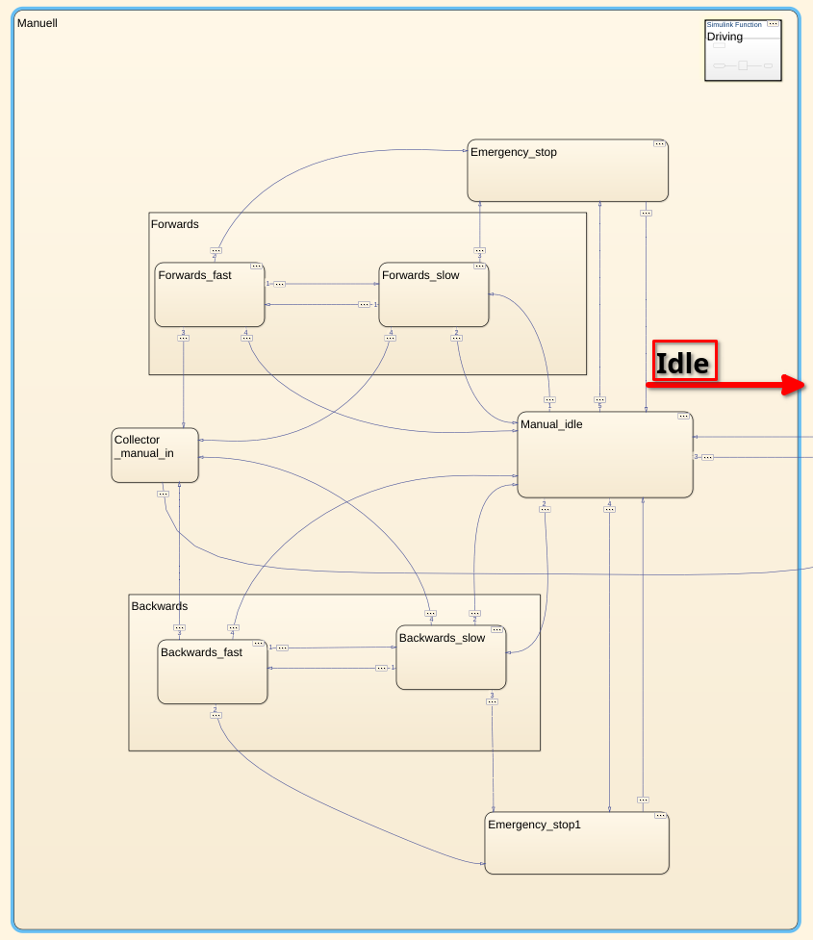
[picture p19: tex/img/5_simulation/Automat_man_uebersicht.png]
		
		\caption{Automat – Übersicht der manuellen Steuerung}
		\label{Automat_man:img:man_übersicht}
	\end{center}
\end{figure}
\pagebreak[1]

\pagebreak[1]
\begin{table}[!ht]
	\centering
	\caption{Ausgänge – der Zustände \frqq Forwards\flqq\ und \frqq Backwards\flqq\ –  \frqq slow\flqq}
	\label{Automat_man:tab:z_V_langsam}
	\begin{tabular}{llcc}
		\hline
		\textbf{Ausgänge}                             & \makecell{\textbf{I/O Module}             \\ \textbf{IO397-50k}}     & \makecell{\textbf{Werte}       \\ \textbf{\frqq Forwards\flqq}} & \makecell{\textbf{Werte}     \\ \textbf{\frqq Backwards\flqq}}  \\ \hline
		\multicolumn{1}{l|}{speed out=Driving$(1,5)$} & \multicolumn{1}{l|}{A1}       & 1,5 & 1,5 \\
		\multicolumn{1}{l|}{break motor out}          & \multicolumn{1}{l|}{B3}       & 1   & 1   \\
		\multicolumn{1}{l|}{direction out}            & \multicolumn{1}{l|}{B4}       & 5   & 0   \\
		\multicolumn{1}{l|}{cruise out}               & \multicolumn{1}{l|}{B5}       & 5   & 5   \\
		\multicolumn{1}{l|}{break mechanically out}   & \multicolumn{1}{l|}{B6}       & 0   & 0   \\
		\multicolumn{1}{l|}{emergency stop out}       & \multicolumn{1}{l|}{B7}       & 0   & 0   \\ \hline
	\end{tabular}
\end{table}
\pagebreak[1]

\pagebreak[1]
\begin{table}[!ht]
	\centering
	\caption{Ausgänge – der Zustände \frqq Forwards\flqq\ und \frqq Backwards\flqq\ –  \frqq fast\flqq}
	\label{Automat_man:tab:z_V_schnell}
	\begin{tabular}{cccc}
		\hline
		\textbf{Ausgänge}                           & \makecell{\textbf{I/O Module}         \\ \textbf{IO397-50k}}    & \makecell{\textbf{Werte}     \\ \textbf{\frqq Forwards\flqq}} & \makecell{\textbf{Werte}     \\ \textbf{\frqq Backwards\flqq}} \\ \hline
		\multicolumn{1}{l|}{speed out=Driving$(3)$} & \multicolumn{1}{l|}{A1}       & 3 & 3 \\
		\multicolumn{1}{l|}{break motor out}        & \multicolumn{1}{l|}{B3}       & 1 & 1 \\
		\multicolumn{1}{l|}{direction out}          & \multicolumn{1}{l|}{B4}       & 5 & 0 \\
		\multicolumn{1}{l|}{cruise out}             & \multicolumn{1}{l|}{B5}       & 5 & 5 \\
		\multicolumn{1}{l|}{break mechanically out} & \multicolumn{1}{l|}{B6}       & 0 & 0 \\
		\multicolumn{1}{l|}{emergency stop out}     & \multicolumn{1}{l|}{B7}       & 0 & 0 \\ \hline
	\end{tabular}
\end{table}
\pagebreak[1]

\pagebreak[1]
\begin{figure}[!ht]
	\begin{center}
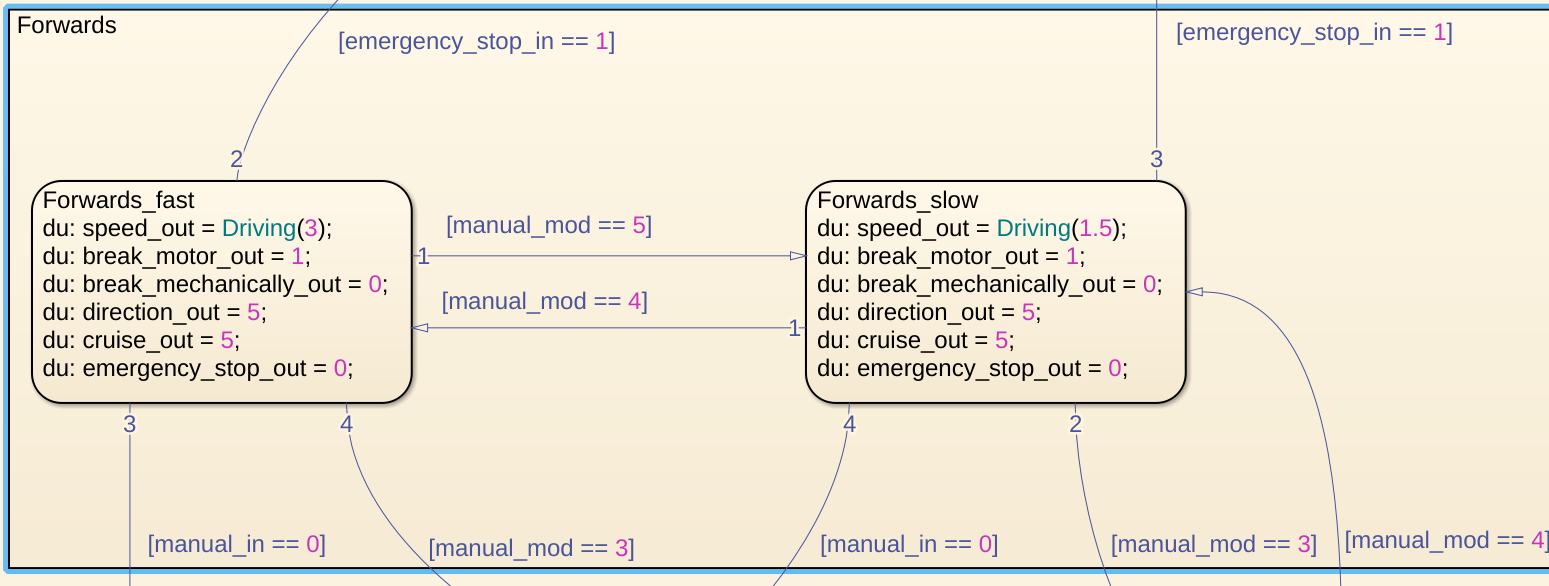
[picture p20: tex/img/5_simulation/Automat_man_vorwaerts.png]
		
		\caption{Automat – \frqq Forwards\flqq\ -Stateflow der manuellen Steuerung}
		\label{Automat_man:img:man_vorwärts}
	\end{center}
\end{figure}
\pagebreak[1]

Mit dem Wahltaster (siehe Tabelle \ref{Controlpanel:tab:Wahlschalter}) kann zwischen den Zuständen gewechselt werden. In der Abbildung \ref{Automat_man:img:man_vorwärts} ist der Ausschnitt des \frqq Forwards\flqq\ -Stateflow zu sehen. Wenn sich der Automat in dem Stateflow \frqq Forwards\flqq\ befindet, gibt es keine direkte Verknüpfung zu dem \frqq Backwards\flqq\ Stateflow, somit muss man erst in den Zustand \frqq Manual idle\flqq\ wechseln, um in den Stateflow \frqq Backwards\flqq\ zu gelangen.

Der Zustand \frqq Collector manual in\flqq\ fängt  das Schaltsignal des Wahlschalters ab, wenn mitten im Betrieb auf Automatik geschalten wird und führt in dem \frqq Idle \flqq\ Zustand.

\subsubsection{Automat für die automatische Steuerung}
\label{Automatensteuerung:Automat_auto}

Die automatische Steuerung soll das Fahrzeug innerhalb der Röhre bis zur eingestellten Geschwindigkeit beschleunigen. Ab einer bestimmten Distanz zum Ende der Röhre soll es allmählich abbremsen und schließlich zum Stillstand kommen.

Der Automat \frqq Automatic\flqq\ besteht aus den Zuständen \frqq Automatic\flqq, \frqq Drive\flqq, \frqq Distance\flqq, \frqq Stop\flqq\ und \frqq Emergency stop\flqq, die in Abbildung \ref{Automat:img:auto_übersicht} dargestellt sind.\\
Der Zustand \frqq Automatic\flqq\ beschreibt den Idle-Zustand der automatischen Steuerung. Von hier aus wird der Zustand \frqq Drive\flqq\ angesteuert, sobald der Startknopf des \frqq Control Panels\flqq\ (siehe Abbildung \ref{Controlpanel:img:Controlpanel}) betätigt wird. Die Ausgänge werden gemäß Tabelle \ref{Automat_man:tab:automatic} gesetzt, solange der Zustand \frqq Automatic\flqq\ nicht verlassen wird.\\
Im Zustand \frqq Drive\flqq\ wird die Geschwindigkeit vom Nutzer mittels des Drehrads \frqq Geschwindigkeit Automatik\flqq\ eingestellt. Wird hingegen der \frqq Stop\flqq\ Taster betätigt, wird der Zustand \frqq Stop\flqq\ angesteuert. Ab einer Distanz von 10 m wird der Zustand \frqq Distance\flqq\ aktiviert. In Tabelle \ref{Automat_man:tab:drive} sind die Ausgänge des Zustands \frqq Drive\flqq\ dargestellt.\\
Wie bereits erwähnt, wird die Geschwindigkeit in Abhängigkeit vom Abstand \frqq distance\flqq\ zum Ende der Röhre verringert, hierbei wird in dem Zustand \frqq Distance\flqq\ der Augang der Geschwindigkeit mittels folgender Gleichung ermittelt:

\pagebreak[1]
\begin{align}
	\label{eq:speedout}
	speed_{out} = distance_{in}\cdot\frac{speed_{in}-1}{distance}+1
\end{align}
\pagebreak[1]

Soll die Automatik beendet werden, kann dies über den Stopp-Taster auf dem Control Panel ausgelöst werden. Dabei werden die in Tabelle \ref{Automat_man:tab:stop} aufgeführten Signale geschaltet.

\pagebreak[1]
\begin{table}[!ht]
	\centering
	\caption{Ausgänge – Automatic}
	\label{Automat_man:tab:automatic}
	\begin{tabular}{lll}
		\hline
		\textbf{Ausgänge}                           & \makecell{\textbf{I/O Module}             \\ \textbf{IO397-50k}}                 & \textbf{Wert} \\ \hline
		\multicolumn{1}{l|}{speed out}              & \multicolumn{1}{l|}{A1}       & Driving() \\
		\multicolumn{1}{l|}{Driving(1)}             & \multicolumn{1}{l|}{}         & Reset     \\
		\multicolumn{1}{l|}{break motor out}        & \multicolumn{1}{l|}{B3}       & 5         \\
		\multicolumn{1}{l|}{direction out}          & \multicolumn{1}{l|}{B4}       & 5         \\
		\multicolumn{1}{l|}{cruise out}             & \multicolumn{1}{l|}{B5}       & 5         \\
		\multicolumn{1}{l|}{break mechanically out} & \multicolumn{1}{l|}{B6}       & 5         \\
		\multicolumn{1}{l|}{emergency stop out}     & \multicolumn{1}{l|}{B7}       & 5         \\ \hline
	\end{tabular}
\end{table}
\pagebreak[2]

\pagebreak[1]
\begin{table}[!ht]
	\centering
	\caption{Ausgänge – Drive}
	\label{Automat_man:tab:drive}
	\begin{tabular}{lll}
		\hline
		\textbf{Ausgänge}                           & \makecell{\textbf{I/O Module}                     \\ \textbf{IO397-50k}}                 & \textbf{Wert} \\ \hline
		\multicolumn{1}{l|}{speed out}              & \multicolumn{1}{l|}{A1}       & Driving(speed in) \\
		\multicolumn{1}{l|}{Driving(speed in)}      & \multicolumn{1}{l|}{}         & speed in          \\
		\multicolumn{1}{l|}{break motor out}        & \multicolumn{1}{l|}{B3}       & 5                 \\
		\multicolumn{1}{l|}{direction out}          & \multicolumn{1}{l|}{B4}       & 5                 \\
		\multicolumn{1}{l|}{cruise out}             & \multicolumn{1}{l|}{B5}       & 5                 \\
		\multicolumn{1}{l|}{break mechanically out} & \multicolumn{1}{l|}{B6}       & 5                 \\
		\multicolumn{1}{l|}{emergency stop out}     & \multicolumn{1}{l|}{B7}       & 5                 \\ \hline
	\end{tabular}
\end{table}
\pagebreak[2]

\pagebreak[1]
\begin{table}[!ht]
	\centering
	\caption{Ausgänge – Distance}
	\label{Automat_man:tab:distance}
	\begin{tabular}{lll}
		\hline
		\textbf{Ausgänge}                           & \makecell{\textbf{I/O Module}                         \\ \textbf{IO397-50k}}                 & \textbf{Wert} \\ \hline
		\multicolumn{1}{l|}{speed out}              & \multicolumn{1}{l|}{A1}       & gl. \ref{eq:speedout} \\
		\multicolumn{1}{l|}{Driving(1)}             & \multicolumn{1}{l|}{}         & distance in           \\
		\multicolumn{1}{l|}{break motor out}        & \multicolumn{1}{l|}{B3}       & 1                     \\
		\multicolumn{1}{l|}{direction out}          & \multicolumn{1}{l|}{B4}       & 5                     \\
		\multicolumn{1}{l|}{cruise out}             & \multicolumn{1}{l|}{B5}       & 5                     \\
		\multicolumn{1}{l|}{break mechanically out} & \multicolumn{1}{l|}{B6}       & 0                     \\
		\multicolumn{1}{l|}{emergency stop out}     & \multicolumn{1}{l|}{B7}       & 0                     \\ \hline
	\end{tabular}
\end{table}
\pagebreak[2]

\pagebreak[1]
\begin{table}[!ht]
	\centering
	\caption{Ausgänge – Stop}
	\label{Automat_man:tab:stop}
	\begin{tabular}{lll}
		\hline
		\textbf{Ausgänge}                           & \makecell{\textbf{I/O Module}             \\ \textbf{IO397-50k}}                 & \textbf{Wert} \\ \hline
		\multicolumn{1}{l|}{speed out}              & \multicolumn{1}{l|}{A1}       & Driving() \\
		\multicolumn{1}{l|}{Driving(Reset)}         & \multicolumn{1}{l|}{}         & Reset     \\
		\multicolumn{1}{l|}{break motor out}        & \multicolumn{1}{l|}{B3}       & 1         \\
		\multicolumn{1}{l|}{direction out}          & \multicolumn{1}{l|}{B4}       & 5         \\
		\multicolumn{1}{l|}{cruise out}             & \multicolumn{1}{l|}{B5}       & 5         \\
		\multicolumn{1}{l|}{break mechanically out} & \multicolumn{1}{l|}{B6}       & 0         \\
		\multicolumn{1}{l|}{emergency stop out}     & \multicolumn{1}{l|}{B7}       & 0         \\ \hline
	\end{tabular}
\end{table}
\pagebreak[2]

\pagebreak[1]
\begin{figure}[!ht]
	\begin{center}
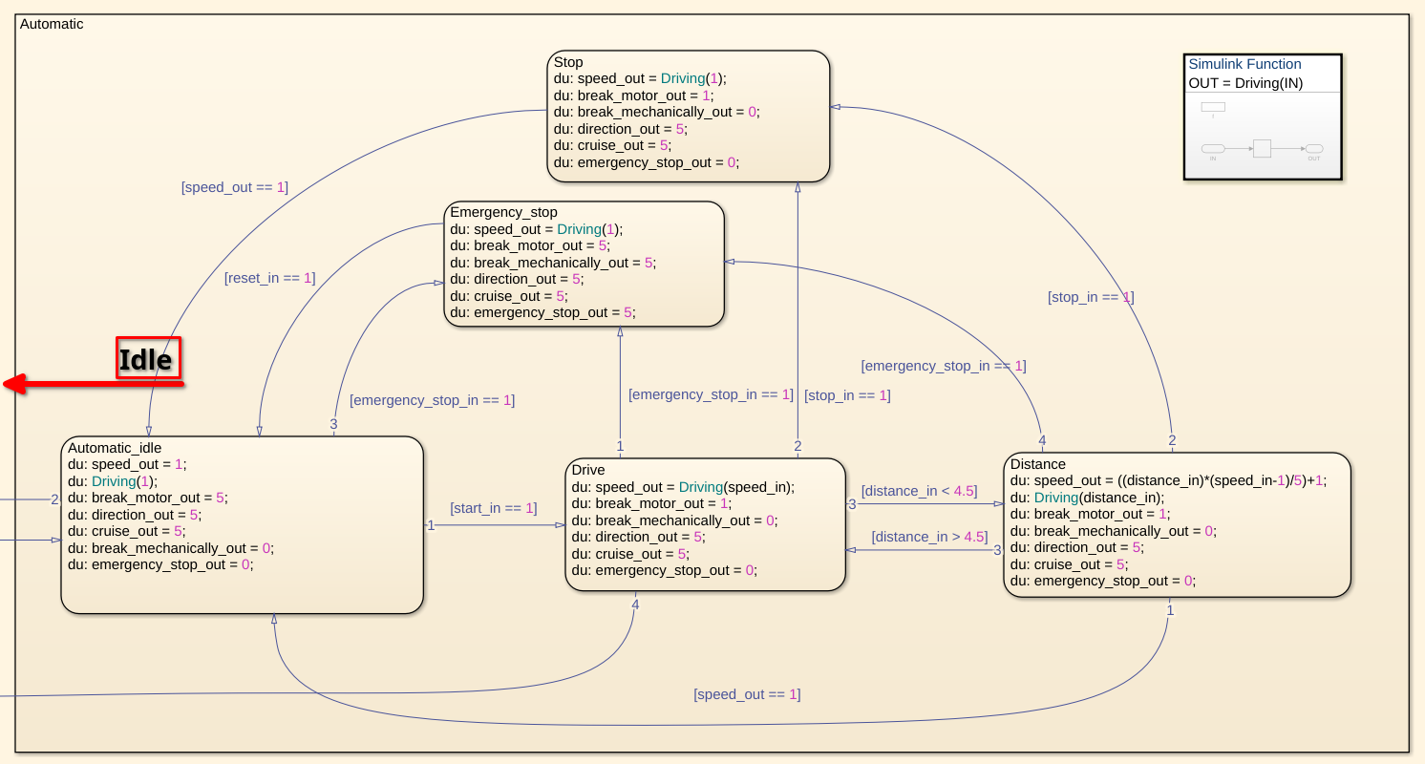
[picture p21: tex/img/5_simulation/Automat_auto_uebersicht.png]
		
		\caption{Automat – Übersicht der automatischen Steuerung}
		\label{Automat:img:auto_übersicht}
	\end{center}
\end{figure}
\pagebreak[4]
\
%%%%%%%%%%%%%%%%%%%%%%%%%%%%%%%%%%%%%%%%%%%%%%%%%%%%%%%%%%%%%%%%%%%%%%%%%%%%%%%%%%%%
%%%%%%%%%%%%%%%%%%%%%%%%%%%%%%%%%%%%%%%%%%%%%%%%%%%%%%%%%%%%%%%%%%%%%%%%%%%%%%%%%%%%
%%%%%%%%%%%%%%%%%%%%%%%%%%%%%%%%%%%%%%%%%%%%%%%%%%%%%%%%%%%%%%%%%%%%%%%%%%%%%%%%%%%%
%%%%%%%%%%%%%%%%%%%%%%%%%%%%%%%%%%%%%%%%%%%%%%%%%%%%%%%%%%%%%%%%%%%%%%%%%%%%%%%%%%%%
%%%%%%%%%%%%%%%%%%%%%%%%%%%%%%%%%%%%%%%%%%%%%%%%%%%%%%%%%%%%%%%%%%%%%%%%%%%%%%%%%%%%
%%%%%%%%%%%%%%%%%%%%%%%%%%%%%%%%%%%%%%%%%%%%%%%%%%%%%%%%%%%%%%%%%%%%%%%%%%%%%%%%%%%%

\newpage
\section{Distanzmessung}
\label{Distanzmessung}
%
%\myboxy{
%	\begin{itemize}
%		\item + Anschlüsse herauszufinden vier anschlüsse gefunden.
%		\item + Was für Aufgaben haben die Anschlüsse?
%		      \subitem Was für ein Kommunikationsprotokol hat der Sensor?
%		      \subitem Asynchron und seriell mit Baudrate 115200. (Ozilloskop)
%		\item mit einem ESP32 die Sensordaten lesen.
%		\item Nachrichtdekodierung (Controller MCU)
%		      \subitem Ox24 Start (Nachricht start)
%		      \subitem 0x26 Stopp (Nachricht ende)
%		      \subitem 24 30 30 30 33 32 36 30 30 32 39 26 (Stopp signal)
%		      \subitem 24 30 30 30 33 32 36 30 31 33 30 26 (Laser an)
%		      \subitem 24 30 30 30 32 32 31 32 33 26 (Messen)
%	\end{itemize}}{To-do}{\textwidth}
%
%

Ursprünglich wurde ein Sensor von Pepperl+Fuchs für die Distanzmessung angeschafft. Da dieser Sensor jedoch sehr teuer ist und wir nicht das Risiko eines möglichen Schadens im Vakuum eingehen wollten, wurde nach einer kostengünstigen Alternative gesucht.\\
Dafür wurde ein günstiges Entfernungsmessgerät für den Heimbedarf angeschafft und analysiert, ob es für die Anwendung geeignet ist.

\subsection{Verbindung}

Der Sensor ist über ein Flachbandkabel mit der Hauptplatine verbunden, wie in Abbildung \ref{img_2_2:sen_dis_parkside:1} zu sehen ist. Auf der Hauptplatine befinden sich vier ungenutzte Lötstellen. Mithilfe eines Oszilloskops und eines Multimeters wurden die Signale an den Lötstellen analysiert, wobei festgestellt wurde, dass Leitung \frqq 1\flqq\ eine Spannung von 3,3 V führt und Leitung \frqq 4\flqq\ als GND dient. Die Leitungen \frqq 2\flqq\ und \frqq 3\flqq\ übertragen digitale Signale und fungieren als Datenleitungen.

Die Kommunikation kann bei einer zweiadrigen Verbindung entweder synchron oder asynchron erfolgen. Bei synchroner Kommunikation dient eine der Leitungen als Taktleitung (Clock). Bei asynchroner Kommunikation ist eine Leitung der Sender (TX) und die andere der Empfänger (RX). Zur Überprüfung der Kommunikationsart wurde ein Oszillogramm (siehe Abbildung \ref{parkside:ozi:datenübertragung}) aufgenommen. Im Oszillogramm wurde kein Taktsignal festgestellt, sodass die Datenübertragung asynchron und Vollduplex erfolgt. In Tabelle \ref{parkside:pinmapping} ist die Pinbelegung aufgelistet.\\

\pagebreak[1]
\begin{figure}[!ht]
	\begin{center}
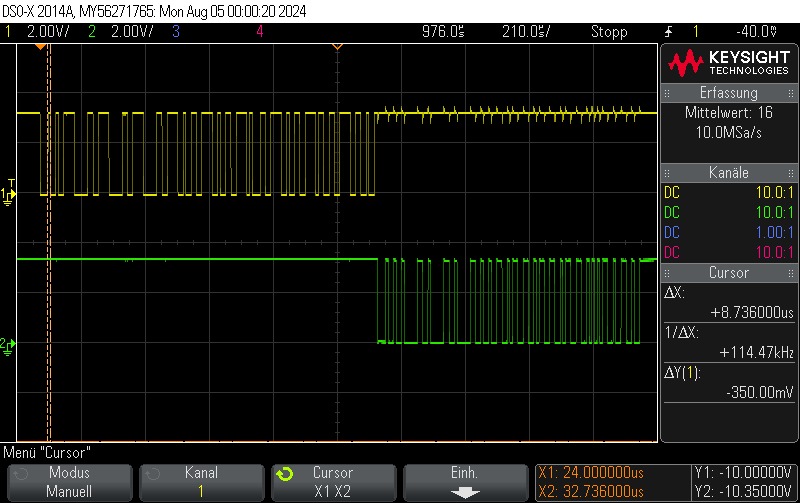
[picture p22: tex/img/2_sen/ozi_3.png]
		
		\caption{Messung – zur Überprüfung der Kommunikationsart: Synchron oder Asynchron}
		\label{parkside:ozi:datenübertragung}
	\end{center}
\end{figure}
\pagebreak[1]

\pagebreak[1]
\begin{table}[!ht]
	\centering
	\caption{PARKSIDE – Pin Mapping – Distanzsensor}
	\label{parkside:pinmapping}
	\begin{tabular}{l|ll}
		\hline
		\textbf{Pin} & \textbf{Farbe} & \textbf{Funktion} \\ \hline
		1            & Rot            & 3V3               \\
		2            & Weiß           & RX (receiver)     \\
		3            & Gelb           & TX (transmitter)  \\
		4            & Schwarz        & GND               \\ \hline
	\end{tabular}
\end{table}
\pagebreak[1]

\pagebreak[1]
\begin{figure}[!ht]
	\begin{center}
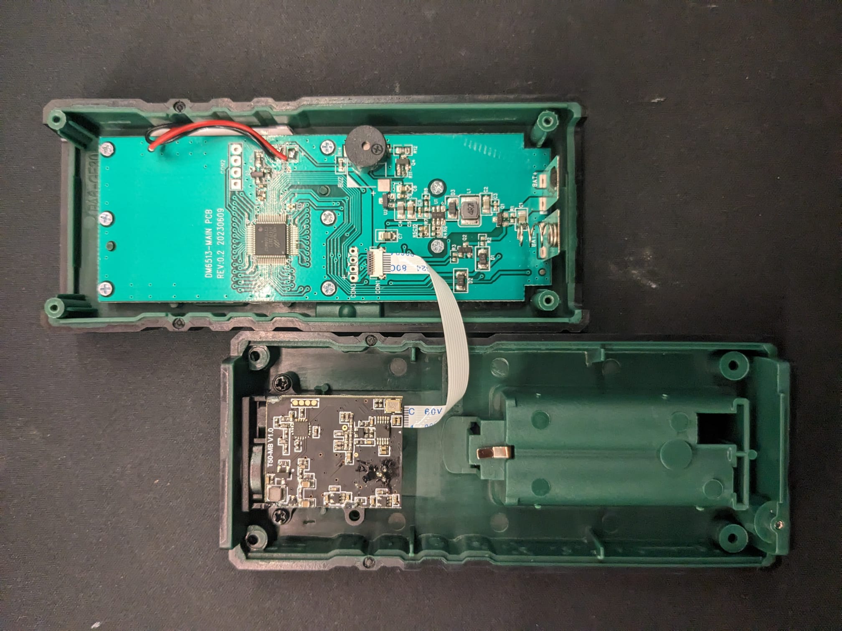
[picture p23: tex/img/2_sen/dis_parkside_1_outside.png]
		
		\caption{PARKSIDE – Distanzsensor – Innenaufbau}
		\label{img_2_2:sen_dis_parkside:1}
	\end{center}
\end{figure}
\pagebreak[4]

\subsection{Dekodierung der Steuersignale}
\label{Distanzmessung:Kodierung}
Um die Steuersignale zu analysieren, wurden die mit dem Oszilloskop aufgenommenen Messwerte in den Tabellen \ref{Steuerung:tab:TX1}, \ref{Steuerung:tab:RX1} und \ref{Steuerung:tab:RX2} dokumentiert. Bei den Messungen fiel auf, dass jede Nachricht mit dem Bitmuster \frqq 0x24\flqq\ (Nachricht-Start) beginnt und mit dem Bitmuster \frqq 0x26\flqq\ (Nachricht-Ende) endet. Zwischen diesen beiden Bitmustern sind die Steuersignale und Messwerte kodiert, welche im Folgenden erklärt werden.\\
\
\pagebreak[1]
\begin{figure}[!ht]
	\begin{center}
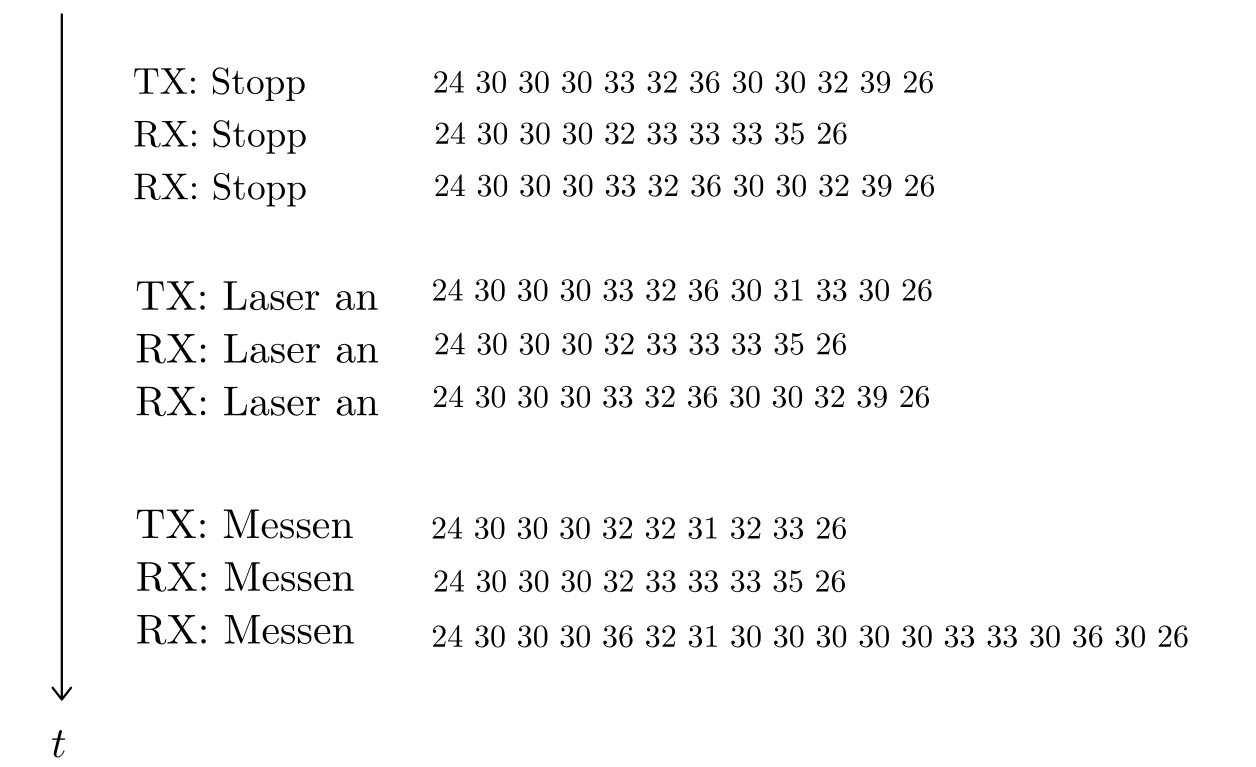
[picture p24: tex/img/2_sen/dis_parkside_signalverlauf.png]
		
		\caption{Distanzmessung – Signalverlauf der Steuersignale}
		\label{Kodierung:pic:signalverlauf}
	\end{center}
\end{figure}
\pagebreak[4]
Die Signalübertragung in den Tabellen ist wie folgt aufgebaut: In Tabelle \ref{Steuerung:tab:TX1} zeigt die Spalte \frqq Stopp\flqq\ die erste Nachricht, die an den Sensor gesendet wird. Der Sensor antwortet stets mit zwei Nachrichten: Die erste Nachricht ist in Tabelle \ref{Steuerung:tab:RX1} dargestellt, die zweite in Tabelle \ref{Steuerung:tab:RX2}, in der Abbildung \ref{Kodierung:pic:signalverlauf} ist der Verlauf noch einmal aufgeführt.\\ \ \\
Die gelb hinterlegten Felder in den Tabellen weisen auf ein identisches Bitmuster hin. Nach jedem Start-Byte werden drei identisch kodierte Bytes gesendet, die als Delay fungieren. Der Sensor antwortet nach jedem \frqq Transmitter\flqq\ Signal mit derselben Kodierung, was als Bestätigung dient, dass er sendebereit ist. Erst wenn das Bitmuster \frqq Messen\flqq\ an den Sensor gesendet wird, überträgt der Sensor die Messdaten, die in den grün hinterlegten Feldern in Tabelle \ref{Steuerung:tab:RX2} als ASCII-Zeichen dargestellt sind.

\pagebreak[4]
\begin{table}[!ht]
	\centering
	\caption{Distanzmessung – Signale die an den Sensor gesendet werden (TX)}
	\label{Steuerung:tab:TX1}
	\begin{tabular}{lllllll}
		\hline
		                        & \multicolumn{2}{c}{TX Stopp} & \multicolumn{2}{c}{ TX Laser an}                   & \multicolumn{2}{c}{TX Messen}                                                                                                                   \\ \hline
		\textbf{Bytes}          & \textbf{Nachricht}           & \textbf{Bdtg.}                                     & \textbf{Nachricht}            & \textbf{Bdtg.}                                     & \textbf{Nachricht}         & \textbf{Bdtg.}                \\ \hline
		\multicolumn{1}{l|}{0}  & \cellcolor[HTML]{9AFF99}24   & \multicolumn{1}{l|}{\cellcolor[HTML]{9AFF99}Start} & \cellcolor[HTML]{9AFF99}24    & \multicolumn{1}{l|}{\cellcolor[HTML]{9AFF99}Start} & \cellcolor[HTML]{9AFF99}24 & \cellcolor[HTML]{9AFF99}Start \\
		\multicolumn{1}{l|}{1}  & \cellcolor[HTML]{FCFF2F}30   & \multicolumn{1}{l|}{\cellcolor[HTML]{FCFF2F}}      & \cellcolor[HTML]{FCFF2F}30    & \multicolumn{1}{l|}{\cellcolor[HTML]{FCFF2F}}      & \cellcolor[HTML]{FCFF2F}30 & \cellcolor[HTML]{FCFF2F}      \\
		\multicolumn{1}{l|}{2}  & \cellcolor[HTML]{FCFF2F}30   & \multicolumn{1}{l|}{\cellcolor[HTML]{FCFF2F}}      & \cellcolor[HTML]{FCFF2F}30    & \multicolumn{1}{l|}{\cellcolor[HTML]{FCFF2F}}      & \cellcolor[HTML]{FCFF2F}30 & \cellcolor[HTML]{FCFF2F}      \\
		\multicolumn{1}{l|}{3}  & \cellcolor[HTML]{FCFF2F}30   & \multicolumn{1}{l|}{\cellcolor[HTML]{FCFF2F}}      & \cellcolor[HTML]{FCFF2F}30    & \multicolumn{1}{l|}{\cellcolor[HTML]{FCFF2F}}      & \cellcolor[HTML]{FCFF2F}30 & \cellcolor[HTML]{FCFF2F}      \\
		\multicolumn{1}{l|}{4}  & 33                           & \multicolumn{1}{l|}{}                              & 33                            & \multicolumn{1}{l|}{}                              & 32                         &                               \\
		\multicolumn{1}{l|}{5}  & 32                           & \multicolumn{1}{l|}{}                              & 32                            & \multicolumn{1}{l|}{}                              & 32                         &                               \\
		\multicolumn{1}{l|}{6}  & 36                           & \multicolumn{1}{l|}{}                              & 36                            & \multicolumn{1}{l|}{}                              & 31                         &                               \\
		\multicolumn{1}{l|}{7}  & 30                           & \multicolumn{1}{l|}{}                              & 30                            & \multicolumn{1}{l|}{}                              & 32                         &                               \\
		\multicolumn{1}{l|}{8}  & 30                           & \multicolumn{1}{l|}{}                              & 31                            & \multicolumn{1}{l|}{}                              & 33                         &                               \\
		\multicolumn{1}{l|}{9}  & 32                           & \multicolumn{1}{l|}{}                              & 33                            & \multicolumn{1}{l|}{}                              & \cellcolor[HTML]{FD6864}26 & \cellcolor[HTML]{FD6864}Stop  \\
		\multicolumn{1}{l|}{10} & 39                           & \multicolumn{1}{l|}{}                              & 30                            & \multicolumn{1}{l|}{}                              &                            &                               \\
		\multicolumn{1}{l|}{11} & \cellcolor[HTML]{FD6864}26   & \multicolumn{1}{l|}{\cellcolor[HTML]{FD6864}Stop}  & \cellcolor[HTML]{FD6864}26    & \multicolumn{1}{l|}{\cellcolor[HTML]{FD6864}Stop}  &                            &                               \\ \hline
	\end{tabular}
\end{table}

\pagebreak[1]
\begin{table}[!ht]
	\centering
	\caption{Distanzmessung – Signale die von dem Sensor gesendet werden 1 (RX)}
	\label{Steuerung:tab:RX1}
	\begin{tabular}{lllllll}
		\hline
		                        & \multicolumn{2}{c}{RX Stopp} & \multicolumn{2}{c}{RX Laser an}                    & \multicolumn{2}{c}{RX Messen}                                                                                                                   \\ \hline
		\textbf{Bytes}          & \textbf{Nachricht}           & \textbf{Bdtg.}                                     & \textbf{Nachricht}            & \textbf{Bdtg.}                                     & \textbf{Nachricht}         & \textbf{Bdtg.}                \\ \hline
		\multicolumn{1}{l|}{0}  & \cellcolor[HTML]{9AFF99}24   & \multicolumn{1}{l|}{\cellcolor[HTML]{9AFF99}Start} & \cellcolor[HTML]{9AFF99}24    & \multicolumn{1}{l|}{\cellcolor[HTML]{9AFF99}Start} & \cellcolor[HTML]{9AFF99}24 & \cellcolor[HTML]{9AFF99}Start \\
		\multicolumn{1}{l|}{1}  & \cellcolor[HTML]{F8FF00}30   & \multicolumn{1}{l|}{\cellcolor[HTML]{F8FF00}}      & \cellcolor[HTML]{F8FF00}30    & \multicolumn{1}{l|}{\cellcolor[HTML]{F8FF00}}      & \cellcolor[HTML]{F8FF00}30 & \cellcolor[HTML]{F8FF00}      \\
		\multicolumn{1}{l|}{2}  & \cellcolor[HTML]{F8FF00}30   & \multicolumn{1}{l|}{\cellcolor[HTML]{F8FF00}}      & \cellcolor[HTML]{F8FF00}30    & \multicolumn{1}{l|}{\cellcolor[HTML]{F8FF00}}      & \cellcolor[HTML]{F8FF00}30 & \cellcolor[HTML]{F8FF00}      \\
		\multicolumn{1}{l|}{3}  & \cellcolor[HTML]{F8FF00}30   & \multicolumn{1}{l|}{\cellcolor[HTML]{F8FF00}}      & \cellcolor[HTML]{F8FF00}30    & \multicolumn{1}{l|}{\cellcolor[HTML]{F8FF00}}      & \cellcolor[HTML]{F8FF00}30 & \cellcolor[HTML]{F8FF00}      \\
		\multicolumn{1}{l|}{4}  & \cellcolor[HTML]{F8FF00}32   & \multicolumn{1}{l|}{\cellcolor[HTML]{F8FF00}}      & \cellcolor[HTML]{F8FF00}32    & \multicolumn{1}{l|}{\cellcolor[HTML]{F8FF00}}      & \cellcolor[HTML]{F8FF00}32 & \cellcolor[HTML]{F8FF00}      \\
		\multicolumn{1}{l|}{5}  & \cellcolor[HTML]{F8FF00}33   & \multicolumn{1}{l|}{\cellcolor[HTML]{F8FF00}}      & \cellcolor[HTML]{F8FF00}33    & \multicolumn{1}{l|}{\cellcolor[HTML]{F8FF00}}      & \cellcolor[HTML]{F8FF00}33 & \cellcolor[HTML]{F8FF00}      \\
		\multicolumn{1}{l|}{6}  & \cellcolor[HTML]{F8FF00}33   & \multicolumn{1}{l|}{\cellcolor[HTML]{F8FF00}}      & \cellcolor[HTML]{F8FF00}33    & \multicolumn{1}{l|}{\cellcolor[HTML]{F8FF00}}      & \cellcolor[HTML]{F8FF00}33 & \cellcolor[HTML]{F8FF00}      \\
		\multicolumn{1}{l|}{7}  & \cellcolor[HTML]{F8FF00}33   & \multicolumn{1}{l|}{\cellcolor[HTML]{F8FF00}}      & \cellcolor[HTML]{F8FF00}33    & \multicolumn{1}{l|}{\cellcolor[HTML]{F8FF00}}      & \cellcolor[HTML]{F8FF00}33 & \cellcolor[HTML]{F8FF00}      \\
		\multicolumn{1}{l|}{8}  & \cellcolor[HTML]{F8FF00}35   & \multicolumn{1}{l|}{\cellcolor[HTML]{F8FF00}}      & \cellcolor[HTML]{F8FF00}35    & \multicolumn{1}{l|}{\cellcolor[HTML]{F8FF00}}      & \cellcolor[HTML]{F8FF00}35 & \cellcolor[HTML]{F8FF00}      \\
		\multicolumn{1}{l|}{9}  & \cellcolor[HTML]{FD6864}26   & \multicolumn{1}{l|}{\cellcolor[HTML]{FD6864}Stop}  & \cellcolor[HTML]{FD6864}26    & \multicolumn{1}{l|}{\cellcolor[HTML]{FD6864}Stop}  & \cellcolor[HTML]{FD6864}26 & \cellcolor[HTML]{FD6864}Stop  \\
		\multicolumn{1}{l|}{10} &                              & \multicolumn{1}{l|}{}                              &                               & \multicolumn{1}{l|}{}                              &                            &                               \\
		\multicolumn{1}{l|}{11} &                              & \multicolumn{1}{l|}{}                              &                               & \multicolumn{1}{l|}{}                              &                            &                               \\ \hline
	\end{tabular}
\end{table}
\pagebreak[1]
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

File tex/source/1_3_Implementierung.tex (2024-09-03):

\chapter{Implementierung}

\section{Bauteile}

Für das Projekt wurde der die echtzeitfähige steuerung, Batterie,  Motor und dem dazugöhrige Steuerung vorgeben.  Alle weiteren Bauteile mussten bestellt werden.

\section{Schaltplan}

\myboxy{
	\begin{itemize}
		\item Funktion (=Anlage) und Ortskennzeichen (+Ort) definieren. Funktionlen Engineering
		\item Bauteilbezeichnung (BMK)
		\item Aderfarben und Querschnitt definieren.
		\item Ausgesuchte Bauteile in die Schaltung hinzufügen.
		\item Bauteile, die es nicht gibt, selber erstellen.
		      \subitem Bauteile sortiert hinzufügen. Spannungsversorung, Steuerung(In dann 0ut), Lastkreis und Sonderfunktionen.
	\end{itemize}}{To-do}{\textwidth}

Zu Beginn der Erstellung des Schaltplans sollten die Funktions- und Ortskennzeichen festgelegt werden, ebenso die Beschriftung der Bauteile und Leitungen. Für die Verdrahtung müssen den Potenzialen entsprechende Aderfarben zugewiesen werden.

\subsection{Betriebsmittelbezeichnung}

Ein Betriebsmittel besteht aus verschiedenen Kennzeichen: dem Funktionskennzeichen (=), dem Ortskennzeichen (+) und dem Betriebsmittelkennzeichen (-). Früher wurde das Funktionskennzeichen als „Anlage“ bezeichnet. In der neuen DIN EN IEC 81346-2 \cite{DIN_EN_IEC_81346-2} wurde diese Bezeichnung jedoch auf „Funktion“ geändert.

Das Funktionskennzeichen beschreibt eine bestimmte Funktion im Schaltplan, wie beispielsweise die Spannungsversorgung oder die Steuerung (siehe Tabelle \ref{bmk:funktionskennzeichen}).

\begin{table}[!ht]
	\centering
	\caption{Schaltplan – Funktionskennzeichen (=)}
	\label{bmk:funktionskennzeichen}
	\begin{tabular}{ll}
		\hline
		\textbf{Abkürzung}      & \textbf{Bezeichnung} \\ \hline
		\multicolumn{1}{l|}{SV} & Spannungsversorung   \\
		\multicolumn{1}{l|}{SE} & Steuerung eingänge   \\
		\multicolumn{1}{l|}{SA} & Steuerung ausgänge   \\
		\multicolumn{1}{l|}{KO} & Kommunikation        \\
		\multicolumn{1}{l|}{AT} & Antrieb              \\
		\multicolumn{1}{l|}{NA} & Not-Aus              \\ \hline
	\end{tabular}
\end{table}

Das Ortskennzeichen gibt an, an welchem Ort ein Bauteil installiert ist. Beispielsweise gibt es im Pod eine Kontrolleinheit und eine Batterieeinheit. Im Schaltplan wird dadurch deutlich, welche Verbindungen zwischen verschiedenen Orten bestehen. Das Ortskennzeichen erleichtert zudem die Wartung und Installation des Systems.

\begin{table}[!ht]
	\centering
	\caption{Schaltplan – Ortskennzeichen (+)}
	\label{bmk:ortskennzeichen}
	\begin{tabular}{ll}
		\hline
		\textbf{Abkürzung}      & \textbf{Bezeichnung} \\ \hline
		\multicolumn{1}{l|}{BE} & Batterieeinheit      \\
		\multicolumn{1}{l|}{KE} & Kontrolleinheit      \\
		\multicolumn{1}{l|}{AE} & Antriebseinheit      \\ \hline
	\end{tabular}
\end{table}

\begin{figure}[!ht]
	\begin{center}
		
		\caption{Schaltplan – Aufbauplan}
		\label{img_3_2:aufbauplan:1}
	\end{center}
\end{figure}

Das Betriebsmittelkennzeichen schließlich bezeichnet das spezifische Bauteil. Die genaue Zuordnung der Bezeichnungen ist in der DIN EN IEC 81346-2 geregelt. Die für das Projekt relevanten Betriebsmittelkennzeichen sind in Tabelle \ref{bmk:betriebsmittelkennzeichen} aufgeführt.
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

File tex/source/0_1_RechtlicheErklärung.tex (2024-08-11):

\chapter*{Rechtliche Erklärung}
\label{sec:Declaration} %
\addcontentsline{toc}{section}{Rechtliche Erklärung}

\section*{Erklärung}
\begin{itemize}
	\item[ {[\sout{~ja}|nein~]} ] Die vorliegende Arbeit enthält vertrauliche / kommerziell nutzbare Informationen, deren Rechte außerhalb der Hochschule Emden/Leer liegen.
	      Sie darf nur den am Prüfungsverfahren beteiligten Personen zugänglich gemacht werden, die hiermit auf ihre Pflicht zur Vertraulichkeit hingewiesen werden (Sperrvermerk).

	\item[ {[~ja|\sout{nein~}]} ] Soweit meine Rechte berührt sind, erkläre ich mich einverstanden, dass die vorliegende Arbeit Angehörigen der Hochschule Emden/Leer für Studium / Lehre / Forschung uneingeschränkt zugänglich gemacht werden kann.

\end{itemize}

%\hfill Nicht Zutreffendes bitte streichen.

\section*{Eidesstattliche Versicherung}

Ich, der Unterzeichnende, erkläre hiermit an Eides statt, dass ich die vorliegende Arbeit selbstständig verfasst und keine anderen als die angegebenen Quellen und Hilfsmittel benutzt habe.
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

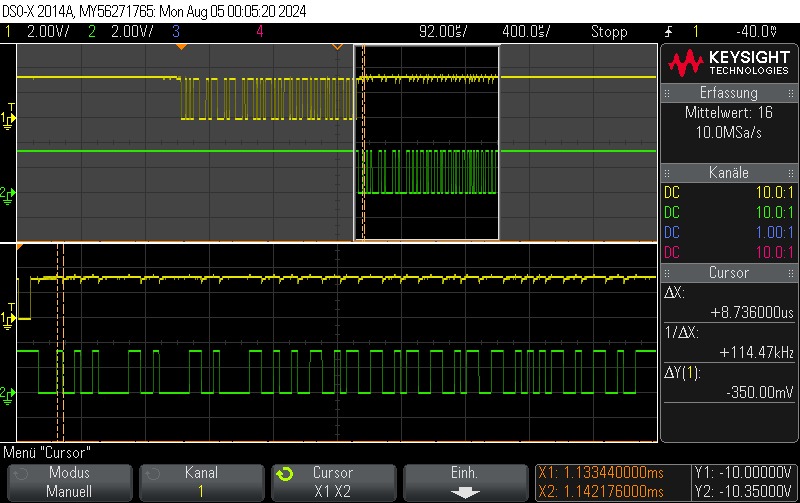
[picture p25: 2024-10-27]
tex/img/2_sen/ozi_6.png

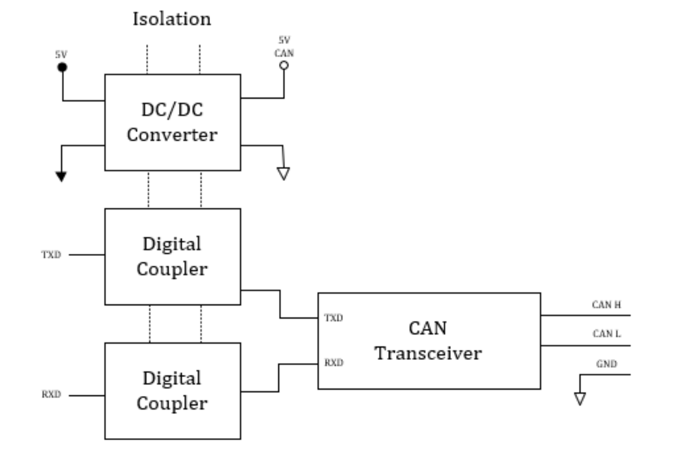
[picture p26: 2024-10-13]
tex/img/4_simulink/IO691_Galvanic_isolation.png

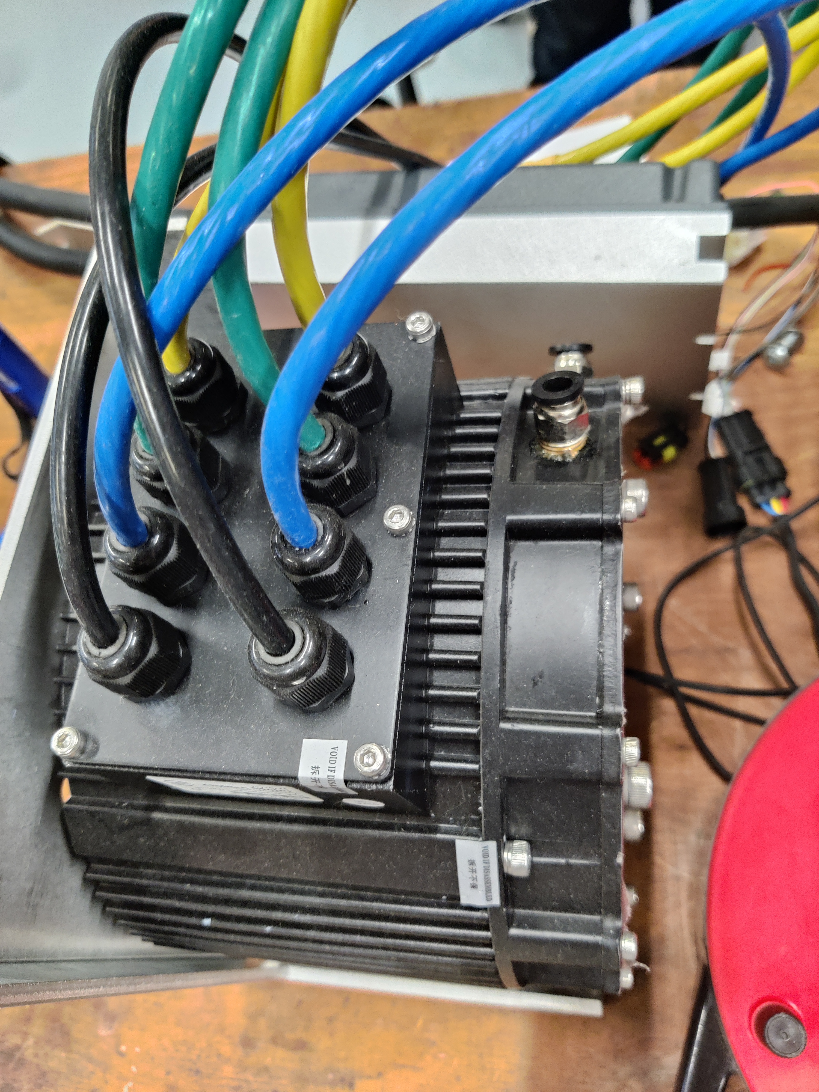
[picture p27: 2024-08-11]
tex/img/2_imp/2_pic_bldc_motor.png

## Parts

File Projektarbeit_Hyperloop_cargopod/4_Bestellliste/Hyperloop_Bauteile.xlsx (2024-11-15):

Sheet: Alle_Bauteile
Verwendung | Anlage | Ort | BMK | Typ | Anzahl | Beschreibung | Hersteller | Bezeichnung | EAN | Hersteller-Nr | Preis | Status | Link | Total EUR
Actor | 1P1 | 1B1 |  | Batterie | 3 | 50Ah | 51,2V | 2560Wh | DeepCPower | Lithium LiFePO4 Marine/Boot Batterie | 4250561726451 |  | 1720.00 € | Vorhanden | https://cs-batteries.de/50Ah-512V-2560Wh-Lithium-LiFePO4-Marine-Boot-Batterie | 5160.00 €
Actor | 1P1 | 1M1 |  | Motor | 1 | Motor | Glden Motor | 10 KW BLDC Motor Liquid Cooled | - | SKU: 17864008 | 1025.99 € | Vorhanden | https://goldenmotor.bike/product/48-volt-10kw-bldc-motor-liquid-cooled/ | 1025.99 €
Actor | 1P1 | 1M1 |  | VECTOR 500 Series Brushless | 1 | Sinewave Generator | Golden Motor | VECTOR 500 Series Brushless Motor Controller (10 kW Motors) | - | SKU: VEC500-1 | 735.99 € | Vorhanden | https://goldenmotor.bike/product/vector-500-series-72-volt-brushless-motor-controller/ | 735.99 €
Actor | 1P1 | 1C1 |  | Relais Stecker | 10 | Koppelrelais | Weidmüller | Koppelrelais, 5 V DC, 6 A, 1 Wechsler | 4032248904792 | TRS 5VDC 1CO | 13.70 € | Vorhanden | https://www.reichelt.de/koppelrelais-5-v-dc-6-a-1-wechsler-trs-5vdc-1co-p314450.html?trstct=pos_0&nbc=1 | 137.00 €
Beschriftung | 1P1 |  |  | Schrumpfschlauch | 2 | Rot 16.70 mm 8 mm Schrumpfrate:2:1 | TRU COMPONENTS | Schrumpfschlauch | 2050004885156 | 1225452 | 1.08 € | Vorhanden | https://www.conrad.de/de/p/tru-components-1225452-schrumpfschlauch-ohne-kleber-rot-16-70-mm-8-mm-schrumpfrate-2-1-meterware-1570738.html | 2.16 €
Beschriftung | 1P1 |  |  | Schrumpfschlauch | 3 | Schwarz 16.70 mm 8 mm Schrumpfrate:2:1 | TRU COMPONENTS | Schrumpfschlauch | 2050004885187 | 1225519 | 1.08 € | Vorhanden | https://www.conrad.de/de/p/tru-components-1225519-schrumpfschlauch-ohne-kleber-schwarz-16-70-mm-8-mm-schrumpfrate-2-1-meterware-1570742.html | 3.24 €
Beschriftung | 1P1 |  |  | Zackband | 2 | ZBF 5,lgs:1-10 | Phoenix Contact | Zackband | 4017918598846 | 33694.62569 | 6.00 € | Bestellt | https://www.conrad.de/de/p/phoenix-contact-zackband-zbf-5-lgs-1-10-811608726.html | 12.00 €
Beschriftung | 1P1 |  |  | Zackband | 1 | ZBF 5,LGS:FORTL.ZAHLEN 11-20 | Phoenix Contact | Zackband | 4017918598853 | 33694.63264 | 5.82 € | Bestellt | https://www.conrad.de/de/p/phoenix-contact-zackband-zbf-5-lgs-11-20-811608728.html | 5.82 €
Beschriftung | 1P1 |  |  |  | 2 | höhenverstellbar 249-119 | WAGO | Gruppenschildträger | 4017332188371 | 249-119 | 4.45 € | Bestellt | https://www.conrad.de/de/p/wago-gmbh-co-kg-gruppenschildtraeger-hoehenverstellbar-249-119-801316925.html | 8.90 €
Beschriftung | 1P1 |  |  |  | 1 | gelb | AVERY Zweckform | Etiketten 10x25,5 |  | L6037-20 | 9.69 € | Bestellt | https://www.bueroshop24.de/avery-zweckform-etiketten-345843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 | 9.69 €
Beschriftung | 1P1 |  |  |  | 1 | Kabeletiketten |  | Kabelbeschriftung 10x31 |  |  | 8.99 € | Bestellt | https://www.amazon.de/Kabeletiketten-Erkennungsbox-Wiederverwendbare-Kabelmarkierer-Kabelbeschriftung/dp/B0C2PY19X9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 | 8.99 €
Cabel | 1P1 |  |  | Kabel | 1 | USB Programming Cabel | Golden Motor | Vector Large Bldc Controller USB Programming Interface | - | SKU: VEC-USB |  | Vorhanden |  | 0.00 €
Cabel | 1P1 |  |  | H07V-K 1x35mm² | 25 | Schwarz | LAPP | H07V-K 1 x 1 x 50 mm² Schwarz | 2050000207136 | 4521012-1 | 19.99 € | Vorhanden | https://www.conrad.de/de/p/lapp-4521013-1-litze-h07v-k-1-x-50-mm-schwarz-meterware-603050.html | 499.75 €
Cabel | 1P1 |  |  | H07V-K 1x1mm² | 1 | Blau 100 m | LAPP | Litze Multi-Standard SC | 2050000200762 | 4160302 | 62.18 € | Vorhanden | https://www.conrad.de/de/p/lapp-4160302-litze-multi-standard-sc-2-1-1-x-1-mm-blau-100-m-601559.html | 62.18 €
Cabel | 1P1 |  |  | H07V-K 1x1mm² | 1 | Rot 100 m | LAPP | Litze Multi-Standard SC | 4044774695754 | 4160304 | 63.86 € | Vorhanden | https://www.conrad.de/de/p/lapp-4160304-litze-multi-standard-sc-2-1-1-x-1-mm-rot-100-m-601546.html | 63.86 €
Cabel | 1P1 |  |  | H07V-K 1x1mm² | 1 | Schwarz 100 m | LAPP | Litze Multi-Standard SC | 4044773386820 | 4160301 | 65.54 € | Vorhanden | https://www.conrad.de/de/p/lapp-4160301-litze-multi-standard-sc-2-1-1-x-1-mm-schwarz-100-m-601572.html | 65.54 €
Cabel | 1P1 |  |  | H07V-K 1x1mm² | 1 | Violett 100 m | LAPP | Litze Multi-Standard SC | 4044774695815 | 4160307 | 63.86 € | Vorhanden | https://www.conrad.de/de/p/lapp-4160307-litze-multi-standard-sc-2-1-1-x-1-mm-violett-100-m-601532.html | 63.86 €
Cabel | 1P1 |  |  | Ringkabelschuh | 15 | Unisoliert, innen ø 8mm, max. 35mm², M8 | RS PRO | Ringkabelschuh | 5056111966044 | 2414631 | 1.42 € | Vorhanden | https://www.conrad.de/de/p/rs-pro-ringkabelschuh-unisoliert-innen-o-8mm-max-35mm-m8-805616195.html | 21.30 €
Connector | 1P1 |  |  | Stecker | 9 | Rundsteckverbinder | lumberg | LUM SV 80 Stecker | 4020841550461 |  |  | Vorhanden |  | 0.00 €
Connector | 1P1 |  |  | Buchse | 9 | Einbaukupplung | lumberg | LUM KFV 80 Einbaukupplung | 4020841005558 |  |  | Vorhanden |  | 0.00 €
Connector | 1P1 |  |  | Klemmen | 40 | Klemmen | Phoenix Contact | PT-1,5/S-Quattro grau | 4046356564328 | 3208197 | 0.74 € | Vorhanden | https://www.elektro-wandelt.de/Phoenix-Contact-PT-2-5-QUATTRO-Durchgangsreihenklemme-0-14-4-mm-5-2-mm-grau.html | 29.60 €
Connector | 1P1 |  |  | Klemmen | 2 | Steckbrücke | Phoenix Contact | FBS 5-3,5 | 4046356549226 | 3213043 | 2.05 € | Vorhanden | https://www.elektro-wandelt.de/?cl=details&anid=6745089db873367561fb6a6ea7ee1a3a | 4.10 €
Connector | 1P1 |  |  | Klemmen | 4 | Steckbrücke | Phoenix Contact | FBS 2-3,5 | 4046356549219 | 3213014 | 0.52 € | Vorhanden | https://www.elektro-wandelt.de/Phoenix-Contact-FBS-2-3-5-Steckbruecke-2-polig-rot.html | 2.08 €
Connector | 1P1 |  |  | Klemmen | 3 | Endabdeckung | Phoenix Contact | D-PT 1,5/S-Quattro grau | 4046356564373 | 3208375 | 2.52 € | Offen | https://www.conrad.de/de/p/phoenix-contact-d-pt-endabdeckung-fuer-din-schienen-klemmenbloecke-packung-a-5-stueck-844955206.html | 7.56 €
Connector | 1P1 |  |  |  | 2 | grau | WAGO | Endklammer 6mm | 4017332270823 | 249-116 | 5.60 € | Vorhanden | https://www.conrad.de/de/p/wago-gmbh-co-kg-endklammer-6mm-breit-grau-249-116-802293781.html | 11.20 €
Connector | 1P1 | 1B1 |  | Dose | 2 | 50mm² | REMA | 200A Typ A |  | 76251-00 | 88.55 € | Vorhanden | https://battery-parts.eu/prod/web/Portal-prod-1/artikeldetails.aspx?WPParams=50C9D4C6C5D2E6BDA5A98895A392 | 177.10 €
Connector | 1P1 | 1B1 |  | Ladestecker | 3 | 50mm² | REMA | 200A Typ C |  | 76470-00 | 88.20 € | Vorhanden | https://battery-parts.eu/prod/web/Portal-prod-1/artikeldetails.aspx?WPParams=50C9D4C6C5D2E6BDA5A98895A395 | 264.60 €
Controlbox | 1P1 | 1C1 |  | Schaltkasten | 1 | Schaltkasten | Rittal | KX 1556.000 | 4028177816589 | 1556000 | 59.98 € | Vorhanden | https://www.conrad.de/de/p/rittal-kx-1556-000-installations-gehaeuse-wand-gehaeuse-300-x-400-x-120-stahlblech-lichtgrau-ral-7035-1-st-2251398.html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 | 59.98 €
Controller | 1P1 | 1C1 |  | Echtzeit Steuerung | 2 | Controller | speedgoat | Baseline Real-Time Target Machine | - |  | 12000.00 € | Vorhanden | https://www.speedgoat.com/products-services/real-time-target-machines/baseline-real-time-target-machine | 24000.00 €
Converter | 1P1 | 1C1 |  | Power Module | 1 | - | ANGEEK | ANGEEK 200W 15A DC-DC 8-60V 48V TO 1-36V 5V 12V 24V 19V | - |  | 22.99 € | Vorhanden | https://www.amazon.de/ANGEEK-DC-DC-Converter-Step-down-Module/dp/B07ZH5QDSS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 | 22.99 €
Fuse | 1P1 |  |  | G-Sicherungseinsatz | 1 | G-Sicherungseinsatz | Eska | T 4A 5x20mm 10 Stück |  | 522523 | 2.07 € | Vorhanden | https://www.elektro-wandelt.de/?cl=details&anid=30f8007662a80ff7ce27d548c9a75de0 | 2.07 €
Fuse | 1P1 |  |  | G-Sicherungseinsatz | 1 | G-Sicherungseinsatz | Eska | T 2A 5x20mm 10 Stück |  | X0639149 | 2.07 € | Vorhanden | https://www.elektro-wandelt.de/Eska-522-520-G-Sicherungseinsatz-T-2A-5x20mm-10-Stueck.html | 2.07 €
Fuse | 1P1 |  |  | G-Sicherungseinsatz | 1 | G-Sicherungseinsatz | Eska | T 1A 5x20mm 10 Stück |  | X0639146 | 2.07 € | Vorhanden | https://www.elektro-wandelt.de/Eska-522-517-G-Sicherungseinsatz-T-1A-5x20mm-10-Stueck.html | 2.07 €
Fuse | 1P1 |  |  | Sicherungsklemme mit Leuchtanzeige | 5 | ST 4-HESILED | Phoenix Contact | ST 4-HESILED 24 | 4017918890483 | X0416124 | 13.35 € | Vorhanden | https://www.elektro-wandelt.de/Phoenix-Contact-ST-4-HESILED-24-Sicherungsklemme-mit-Leuchtanzeige.html | 66.75 €
Sensor | 1P1 |  |  | Bescheunigung | 1 | Bescheunigung_2 | DIS Sensor | Beschleunigungssensor 3-axis, ±8g, CAN SIL2/Pld |  | DIS 12205 | 355.50 € | Vorhanden | https://www.reichelt.de/beschleunigungssensor-3-axis-8g-can-sil2-pld-dis-12205-p330041.html?trstct=pos_0&nbc=1 | 355.50 €
Sensor | 1P1 |  |  | Position | 1 | Abstand_2 | Pepperl+Fuchs | VDM28-50-R1-IO-1 |  | VDM28-50-R1-IO-1 | 463.70 € | Vorhanden | https://www.reichelt.de/distanzsensor-0-2-50-m-1x-pnp-npn-1x-analog-m12-vdm28-50-r1-io-1-p276697.html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 | 463.70 €
Sensor | 1P1 |  |  | Temperatur-SWG | 1 | Temp_Sinewavegenerator | Sensorshop24 | Oberflächenfühler mit integrierter Bohrung |  | 012-L7-LP7-NTC5k-2L-5.0 | 10.60 € | Offen | https://www.sensorshop24.de/temperaturfuehler-passiv/oberflaechenfuehler/oberflachenfuehler-mit-integrierter-bohrung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 | 10.60 €
Sensor | 1P1 |  |  | Temperatur-Motor | 1 | Kommt von vom Sinewave Generator |  |  |  |  |  | Vorhanden |  | 0.00 €
Switch | 1P1 |  |  | Hauptschalter | 1 | Hauptschalter | EATON | 041097, 3-pol, 25 A | 4015080410973 | P1-25/EA/SVB | 46.65 € | Vorhanden | https://www.elektro-wandelt.de/?cl=details&anid=0abd8a5b355c3cc1cd0df670924c761f | 46.65 €
Switch | 1P1 | 1C1 |  | Not-Aus | 1 | Not-Aus-Schalter | IDEC | XW1E-BV4TG04MFR | 2050007363033 | XW1E-BV4TG04MFR | 54.21 € | Vorhanden | https://www.conrad.de/de/p/idec-xw1e-bv4tg04mfr-not-aus-schalter-250-v-3-a-4-oeffner-ip65-1-st-2544509.html | 54.21 €
Wifi | 1P1 |  |  | SMA-Kupplung, gewinkelt | 1 |  | BKL | BKL 0409059 SMA-Stecker auf SMA-Kupplung, gewinkelt | 4011376710857 | BKL 0409059 | 6.45 € | Vorhanden | https://www.reichelt.de/sma-stecker-auf-sma-kupplung-gewinkelt-bkl-0409059-p235615.html?trstct=pos_0&nbc=1 | 6.45 €
Wifi | 1P1 |  |  | Antenne | 1 |  | Delock | Delock ZigBee Multi Antenne 88968 WLAN | 4043619889686 | 88968 | 14.22 € | Vorhanden | https://www.conrad.de/de/p/delock-zigbee-multi-antenne-88968-wlan-stab-antenne-4-3-db-2-4-ghz-1421403.html | 14.22 €
Wifi | 1P1 |  |  | Patch-kabel | 1 |  | Renkforce | Renkforce RF-4892528 RJ45 Netzwerkkabel | 4064161191294 | VALUE 21991954 | 1.52 € | Vorhanden | https://www.conrad.de/de/p/renkforce-rf-4892528-rj45-netzwerkkabel-patchkabel-cat-6a-s-ftp-0-50-m-grau-90-nach-unten-gewinkelt-1-st-2446264.html | 1.52 €
Wifi | 1P1 |  |  | SMA-Kabel | 1 |  | SpeaKa Professional Antennen | SpeaKa | 4064161157481 | SP-9226164 | 6.55 € | Vorhanden | https://www.conrad.de/de/p/speaka-professional-antennen-verlaengerungskabel-1x-rp-sma-stecker-1x-rp-sma-buchse-1-00-m-schwarz-2306539.html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 | 6.55 €
Wifi | 1P1 |  |  | Empfänger | 1 | WLAN Access Point | WIENET | WIENET APETHAA | 4049088338571 | 83.040.0051.0 | 269.95 € | Vorhanden | https://www.reichelt.de/wlan-access-point-2-4-ghz-wienet-apethaa-p341778.html?&trstct=pos_1&nbc=1 | 269.95 €
 |  |  |  |  |  |  |  |  |  |  |  |  |  | 0.00 €
 |  |  |  |  |  |  |  |  |  |  |  |  |  | 0.00 €
 |  |  |  |  |  |  |  |  |  |  |  |  |  | 0.00 €
 |  |  |  |  |  |  |  |  |  |  |  |  |  | 0.00 €
 |  |  |  |  |  |  |  |  |  |  |  |  |  | 0.00 €
 |  |  |  |  |  |  |  |  |  |  |  |  |  | 0.00 €
 |  |  |  |  |  |  |  |  |  |  |  |  |  | 0.00 €
 |  |  |  |  |  |  |  |  |  |  |  |  |  | 0.00 €
 |  |  |  |  |  |  |  |  |  |  |  |  |  | 0.00 €
 |  |  |  |  |  |  |  |  |  |  |  |  |  | 0.00 €
 |  |  |  |  |  |  |  |  |  |  |  |  |  | 0.00 €
 |  |  |  |  |  |  |  |  |  |  |  |  |  | 0.00 €
 |  |  |  |  |  |  |  |  |  |  |  |  |  | 0.00 €
 |  |  |  |  |  |  |  |  |  |  |  |  |  | 0.00 €
 |  |  |  |  |  |  |  |  |  |  |  |  |  | 0.00 €
 |  |  |  |  |  |  |  |  |  |  |  |  |  | 0.00 €
 |  |  |  |  |  |  |  |  |  |  |  |  |  | 0.00 €
 |  |  |  |  |  |  |  |  |  |  |  |  |  | 0.00 €
 |  |  |  |  |  |  |  |  |  |  |  |  |  | 0.00 €
 |  |  |  |  |  |  |  |  |  |  |  |  |  | 0.00 €
 |  |  |  |  |  |  |  |  |  |  |  |  |  | 0.00 €
 |  |  |  |  |  |  |  |  |  |  |  |  |  | 0.00 €
 |  |  |  |  |  |  |  |  |  |  |  |  |  | 0.00 €
 |  |  |  |  |  |  |  |  |  |  |  |  |  | 0.00 €
 |  |  |  |  |  |  |  |  |  |  |  |  |  | 0.00 €
 |  |  |  |  |  |  |  |  |  |  |  |  |  | 0.00 €
 |  |  |  |  |  |  |  |  |  |  |  |  |  | 0.00 €
 |  |  |  |  |  |  |  |  |  |  |  |  |  | 0.00 €
 |  |  |  |  |  |  |  |  |  |  |  |  |  | 0.00 €
 |  |  |  |  |  |  |  |  |  |  |  |  |  | 0.00 €
 |  |  |  |  |  |  |  |  |  |  |  |  |  | 0.00 €
 |  |  |  |  |  |  |  |  |  |  |  |  |  | 0.00 €
 |  |  |  |  |  |  |  |  |  |  |  |  |  | 0.00 €
 |  |  |  |  |  |  |  |  |  |  |  |  |  | 0.00 €
 |  |  |  |  |  |  |  |  |  |  |  |  |  | 0.00 €
 |  |  |  |  |  |  |  |  |  |  |  |  |  | 0.00 €
 |  |  |  |  |  |  |  |  |  |  |  |  |  | 0.00 €
 |  |  |  |  |  |  |  |  |  |  |  |  |  | 0.00 €
 |  |  |  |  |  |  |  |  |  |  |  |  |  | 0.00 €
 |  |  |  |  |  |  |  |  |  |  |  |  |  | 0.00 €
 |  |  |  |  |  |  |  |  |  |  |  |  |  | 0.00 €
 |  |  |  |  |  |  |  |  |  |  |  |  |  | 0.00 €
 |  |  |  |  |  |  |  |  |  |  |  |  |  | 0.00 €
 |  |  |  |  |  |  |  |  |  |  |  |  |  | 0.00 €
 |  |  |  |  |  |  |  |  |  |  |  |  |  | 0.00 €
 |  |  |  |  |  |  |  |  |  |  |  |  |  | 0.00 €
 |  |  |  |  |  |  |  |  |  |  |  |  |  | 0.00 €
 |  |  |  |  |  |  |  |  |  |  |  |  |  | 0.00 €
 |  |  |  |  |  |  |  |  |  |  |  |  |  | 0.00 €
 |  |  |  |  |  |  |  |  |  |  |  |  |  | 0.00 €
 |  |  |  |  |  |  |  |  |  |  |  |  |  | 0.00 €
 |  |  |  |  |  |  |  |  |  |  |  |  |  | 0.00 €
 |  |  |  |  |  |  |  |  |  |  |  |  |  | 0.00 €
 |  |  |  |  |  |  |  |  |  |  |  |  |  | 0.00 €
 |  |  |  |  |  |  |  |  |  |  |  |  |  | 0.00 €
 |  |  |  |  |  |  |  |  |  |  |  |  |  | 0.00 €
 |  |  |  |  |  |  |  |  |  |  |  |  |  | 0.00 €
 |  |  |  |  |  |  |  |  |  |  |  |  |  | 0.00 €
 |  |  |  |  |  |  |  |  |  |  |  |  |  | 0.00 €
 |  |  |  |  |  |  |  |  |  |  |  |  |  | 0.00 €
 |  |  |  |  |  |  |  |  |  |  |  |  |  | 0.00 €
 |  |  |  |  |  |  |  |  |  |  |  |  |  | 0.00 €
 |  |  |  |  |  |  |  |  |  |  |  |  |  | 0.00 €
 |  |  |  |  |  |  |  |  |  |  |  |  |  | 0.00 €
 |  |  |  |  |  |  |  |  |  |  |  |  |  | 0.00 €
 |  |  |  |  |  |  |  |  |  |  |  |  |  | 0.00 €
 |  |  |  |  |  |  |  |  |  |  |  |  |  | 0.00 €
 |  |  |  |  |  |  |  |  |  |  |  |  |  | 0.00 €
 |  |  |  |  |  |  |  |  |  |  |  |  |  | 0.00 €
 |  |  |  |  |  |  |  |  |  |  |  |  |  | 0.00 €
 |  |  |  |  |  |  |  |  |  |  |  |  |  | 0.00 €
 |  |  |  |  |  |  |  |  |  |  |  |  |  | 0.00 €
 |  |  |  |  |  |  |  |  |  |  |  |  |  | 0.00 €
 |  |  |  |  |  |  |  |  |  |  |  |  |  | 0.00 €
 |  |  |  |  |  |  |  |  |  |  |  |  |  | 0.00 €
 |  |  |  |  |  |  |  |  |  |  |  |  |  | 0.00 €
 |  |  |  |  |  |  |  |  |  |  |  |  |  | 0.00 €
 |  |  |  |  |  |  |  |  |  |  |  |  |  | 0.00 €
 |  |  |  |  |  |  |  |  |  |  |  |  |  | 0.00 €
 |  |  |  |  |  |  |  |  |  |  |  |  |  | 0.00 €
 |  |  |  |  |  |  |  |  |  |  |  |  |  | 0.00 €
 |  |  |  |  |  |  |  |  |  |  |  |  |  | 0.00 €
 |  |  |  |  |  |  |  |  |  |  |  |  |  | 0.00 €
 |  |  |  |  |  |  |  |  |  |  |  |  |  | 0.00 €
 |  |  |  |  |  |  |  |  |  |  |  |  |  | 0.00 €
 |  |  |  |  |  |  |  |  |  |  |  |  |  | 0.00 €
 |  |  |  |  |  |  |  |  |  |  |  |  |  | 0.00 €
 |  |  |  |  |  |  |  |  |  |  |  |  |  | 0.00 €
 |  |  |  |  |  |  |  |  |  |  |  |  |  | 0.00 €
 |  |  |  |  |  |  |  |  |  |  |  |  |  | 0.00 €
 |  |  |  |  |  |  |  |  |  |  |  |  |  | 0.00 €
 |  |  |  |  |  |  |  |  |  |  |  |  |  | 0.00 €
 |  |  |  |  |  |  |  |  |  |  |  |  |  | 0.00 €
 |  |  |  |  |  |  |  |  |  |  |  |  |  | 0.00 €
 |  |  |  |  |  |  |  |  |  |  |  |  |  | 0.00 €
 |  |  |  |  |  |  |  |  |  |  |  |  |  | 0.00 €
 |  |  |  |  |  |  |  |  |  |  |  |  |  | 0.00 €
 |  |  |  |  |  |  |  |  |  |  |  |  |  | 0.00 €
 |  |  |  |  |  |  |  |  |  |  |  |  |  | 0.00 €
 |  |  |  |  |  |  |  |  |  |  |  |  |  | 0.00 €
 |  |  |  |  |  |  |  |  |  |  |  |  |  | 0.00 €
 |  |  |  |  |  |  |  |  |  |  |  |  |  | 0.00 €
 |  |  |  |  |  |  |  |  |  |  |  |  |  | 0.00 €
 |  |  |  |  |  |  |  |  |  |  |  |  |  | 0.00 €
 |  |  |  |  |  |  |  |  |  |  |  |  |  | 0.00 €
 |  |  |  |  |  |  |  |  |  |  |  |  |  | 0.00 €
 |  |  |  |  |  |  |  |  |  |  |  |  |  | 0.00 €
 |  |  |  |  |  |  |  |  |  |  |  |  |  | 0.00 €
 |  |  |  |  |  |  |  |  |  |  |  |  |  | 0.00 €
 |  |  |  |  |  |  |  |  |  |  |  |  |  | 0.00 €
 |  |  |  |  |  |  |  |  |  |  |  |  |  | 0.00 €
 |  |  |  |  |  |  |  |  |  |  |  |  |  | 0.00 €
 |  |  |  |  |  |  |  |  |  |  |  |  |  | 0.00 €
 |  |  |  |  |  |  |  |  |  |  |  |  |  | 0.00 €
 |  |  |  |  |  |  |  |  |  |  |  |  |  | 0.00 €
 |  |  |  |  |  |  |  |  |  |  |  |  |  | 0.00 €
 |  |  |  |  |  |  |  |  |  |  |  |  |  | 0.00 €
 |  |  |  |  |  |  |  |  |  |  |  |  |  | 0.00 €
 |  |  |  |  |  |  |  |  |  |  |  |  |  | 0.00 €
 |  |  |  |  |  |  |  |  |  |  |  |  |  | 0.00 €
 |  |  |  |  |  |  |  |  |  |  |  |  |  | 0.00 €
 |  |  |  |  |  |  |  |  |  |  |  |  |  | 0.00 €
 |  |  |  |  |  |  |  |  |  |  |  |  |  | 0.00 €
 |  |  |  |  |  |  |  |  |  |  |  |  |  | 0.00 €
 |  |  |  |  |  |  |  |  |  |  |  |  |  | 0.00 €
 |  |  |  |  |  |  |  |  |  |  |  |  |  | 0.00 €
 |  |  |  |  |  |  |  |  |  |  |  |  |  | 0.00 €
 |  |  |  |  |  |  |  |  |  |  |  |  |  | 0.00 €
 |  |  |  |  |  |  |  |  |  |  |  |  |  | 0.00 €
 |  |  |  |  |  |  |  |  |  |  |  |  |  | 0.00 €
 |  |  |  |  |  |  |  |  |  |  |  |  |  | 0.00 €
 |  |  |  |  |  |  |  |  |  |  |  |  |  | 0.00 €
 |  |  |  |  |  |  |  |  |  |  |  |  |  | 0.00 €
 |  |  |  |  |  |  |  |  |  |  |  |  |  | 0.00 €
 |  |  |  |  |  |  |  |  |  |  |  |  |  | 0.00 €
 |  |  |  |  |  |  |  |  |  |  |  |  |  | 0.00 €
 |  |  |  |  |  |  |  |  |  |  |  |  |  | 0.00 €
 |  |  |  |  |  |  |  |  |  |  |  |  |  | 0.00 €
 |  |  |  |  |  |  |  |  |  |  |  |  |  | 0.00 €
 |  |  |  |  |  |  |  |  |  |  |  |  |  | 0.00 €
 |  |  |  |  |  |  |  |  |  |  |  |  |  | 0.00 €
 |  |  |  |  |  |  |  |  |  |  |  |  |  | 0.00 €
 |  |  |  |  |  |  |  |  |  |  |  |  |  | 0.00 €
 |  |  |  |  |  |  |  |  |  |  |  |  |  | 0.00 €
 |  |  |  |  |  |  |  |  |  |  |  |  |  | 0.00 €
 |  |  |  |  |  |  |  |  |  |  |  |  |  | 0.00 €
 |  |  |  |  |  |  |  |  |  |  |  |  |  | 0.00 €
 |  |  |  |  |  |  |  |  |  |  |  |  |  | 0.00 €
 |  |  |  |  |  |  |  |  |  |  |  |  |  | 0.00 €
 |  |  |  |  |  |  |  |  |  |  |  |  |  | 0.00 €
 |  |  |  |  |  |  |  |  |  |  |  |  |  | 0.00 €
 |  |  |  |  |  |  |  |  |  |  |  |  |  | 0.00 €
 |  |  |  |  |  |  |  |  |  |  |  |  |  | 0.00 €
 |  |  |  |  |  |  |  |  |  |  |  |  |  | 0.00 €
 |  |  |  |  |  |  |  |  |  |  |  |  |  | 0.00 €
 |  |  |  |  |  |  |  |  |  |  |  |  |  | 0.00 €
 |  |  |  |  |  |  |  |  |  |  |  |  |  | 0.00 €
 |  |  |  |  |  |  |  |  |  |  |  |  |  | 0.00 €
 |  |  |  |  |  |  |  |  |  |  |  |  |  | 0.00 €
 |  |  |  |  |  |  |  |  |  |  |  |  |  | 0.00 €
 |  |  |  |  |  |  |  |  |  |  |  |  |  | 0.00 €
 |  |  |  |  |  |  |  |  |  |  |  |  |  | 0.00 €
 |  |  |  |  |  |  |  |  |  |  |  |  |  | 0.00 €
 |  |  |  |  |  |  |  |  |  |  |  |  |  | 0.00 €
 |  |  |  |  |  |  |  |  |  |  |  |  |  | 0.00 €
 |  |  |  |  |  |  |  |  |  |  |  |  |  | 0.00 €
 |  |  |  |  |  |  |  |  |  |  |  |  |  | 0.00 €
 |  |  |  |  |  |  |  |  |  |  |  |  |  | 0.00 €
 |  |  |  |  |  |  |  |  |  |  |  |  |  | 0.00 €
 |  |  |  |  |  |  |  |  |  |  |  |  |  | 0.00 €
 |  |  |  |  |  |  |  |  |  |  |  |  |  | 0.00 €
 |  |  |  |  |  |  |  |  |  |  |  |  |  | 0.00 €
 |  |  |  |  |  |  |  |  |  |  |  |  |  | 0.00 €
 |  |  |  |  |  |  |  |  |  |  |  |  |  | 0.00 €
 |  |  |  |  |  |  |  |  |  |  |  |  |  | 0.00 €
 |  |  |  |  |  |  |  |  |  |  |  |  |  | 0.00 €
 |  |  |  |  |  |  |  |  |  |  |  |  |  | 0.00 €
 |  |  |  |  |  |  |  |  |  |  |  |  |  | 0.00 €
 |  |  |  |  |  |  |  |  |  |  |  |  |  | 0.00 €
 |  |  |  |  |  |  |  |  |  |  |  |  |  | 0.00 €
 |  |  |  |  |  |  |  |  |  |  |  |  |  | 0.00 €
 |  |  |  |  |  |  |  |  |  |  |  |  |  | 0.00 €
 |  |  |  |  |  |  |  |  |  |  |  |  |  | 0.00 €
 |  |  |  |  |  |  |  |  |  |  |  |  |  | 0.00 €
 |  |  |  |  |  |  |  |  |  |  |  |  |  | 0.00 €
 |  |  |  |  |  |  |  |  |  |  |  |  |  | 0.00 €
 |  |  |  |  |  |  |  |  |  |  |  |  |  | 0.00 €
 |  |  |  |  |  |  |  |  |  |  |  |  |  | 0.00 €
 |  |  |  |  |  |  |  |  |  |  |  |  |  | 0.00 €
 |  |  |  |  |  |  |  |  |  |  |  |  |  | 0.00 €
 |  |  |  |  |  |  |  |  |  |  |  |  |  | 0.00 €
 |  |  |  |  |  |  |  |  |  |  |  |  |  | 0.00 €
 |  |  |  |  |  |  |  |  |  |  |  |  |  | 0.00 €
 |  |  |  |  |  |  |  |  |  |  |  |  |  | 0.00 €
 |  |  |  |  |  |  |  |  |  |  |  |  |  | 0.00 €
 |  |  |  |  |  |  |  |  |  |  |  |  |  | 0.00 €
 |  |  |  |  |  |  |  |  |  |  |  |  |  | 0.00 €
 |  |  |  |  |  |  |  |  |  |  |  |  |  | 0.00 €
 |  |  |  |  |  |  |  |  |  |  |  |  |  | 0.00 €
 |  |  |  |  |  |  |  |  |  |  |  |  |  | 0.00 €
 |  |  |  |  |  |  |  |  |  |  |  |  |  | 0.00 €
 |  |  |  |  |  |  |  |  |  |  |  |  |  | 0.00 €
 |  |  |  |  |  |  |  |  |  |  |  |  |  | 0.00 €
 |  |  |  |  |  |  |  |  |  |  |  |  |  | 0.00 €
 |  |  |  |  |  |  |  |  |  |  |  |  |  | 0.00 €
 |  |  |  |  |  |  |  |  |  |  |  |  |  | 0.00 €
 |  |  |  |  |  |  |  |  |  |  |  |  |  | 0.00 €
 |  |  |  |  |  |  |  |  |  |  |  |  |  | 0.00 €
 |  |  |  |  |  |  |  |  |  |  |  |  |  | 0.00 €
 |  |  |  |  |  |  |  |  |  |  |  |  |  | 0.00 €
 |  |  |  |  |  |  |  |  |  |  |  |  |  | 0.00 €
 |  |  |  |  |  |  |  |  |  |  |  |  |  | 0.00 €
 |  |  |  |  |  |  |  |  |  |  |  |  |  | 0.00 €
 |  |  |  |  |  |  |  |  |  |  |  |  |  | 0.00 €
 |  |  |  |  |  |  |  |  |  |  |  |  |  | 0.00 €
 |  |  |  |  |  |  |  |  |  |  |  |  |  | 0.00 €
 |  |  |  |  |  |  |  |  |  |  |  |  |  | 0.00 €
 |  |  |  |  |  |  |  |  |  |  |  |  |  | 0.00 €
 |  |  |  |  |  |  |  |  |  |  |  |  |  | 0.00 €
 |  |  |  |  |  |  |  |  |  |  |  |  |  | 0.00 €
 |  |  |  |  |  |  |  |  |  |  |  |  |  | 0.00 €
 |  |  |  |  |  |  |  |  |  |  |  |  |  | 0.00 €
 |  |  |  |  |  |  |  |  |  |  |  |  |  | 0.00 €
 |  |  |  |  |  |  |  |  |  |  |  |  |  | 0.00 €
 |  |  |  |  |  |  |  |  |  |  |  |  |  | 0.00 €
 |  |  |  |  |  |  |  |  |  |  |  |  |  | 0.00 €
 |  |  |  |  |  |  |  |  |  |  |  |  |  | 0.00 €
 |  |  |  |  |  |  |  |  |  |  |  |  |  | 0.00 €
 |  |  |  |  |  |  |  |  |  |  |  |  |  | 0.00 €
 |  |  |  |  |  |  |  |  |  |  |  |  |  | 0.00 €
 |  |  |  |  |  |  |  |  |  |  |  |  |  | 0.00 €
 |  |  |  |  |  |  |  |  |  |  |  |  |  | 0.00 €
 |  |  |  |  |  |  |  |  |  |  |  |  |  | 0.00 €
 |  |  |  |  |  |  |  |  |  |  |  |  |  | 0.00 €
 |  |  |  |  |  |  |  |  |  |  |  |  |  | 0.00 €
 |  |  |  |  |  |  |  |  |  |  |  |  |  | 0.00 €
 |  |  |  |  |  |  |  |  |  |  |  |  |  | 0.00 €
 |  |  |  |  |  |  |  |  |  |  |  |  |  | 0.00 €
 |  |  |  |  |  |  |  |  |  |  |  |  |  | 0.00 €
 |  |  |  |  |  |  |  |  |  |  |  |  |  | 0.00 €
 |  |  |  |  |  |  |  |  |  |  |  |  |  | 0.00 €
 |  |  |  |  |  |  |  |  |  |  |  |  |  | 0.00 €
 |  |  |  |  |  |  |  |  |  |  |  |  |  | 0.00 €
 |  |  |  |  |  |  |  |  |  |  |  |  |  | 0.00 €
 |  |  |  |  |  |  |  |  |  |  |  |  |  | 0.00 €
 |  |  |  |  |  |  |  |  |  |  |  |  |  | 0.00 €
 |  |  |  |  |  |  |  |  |  |  |  |  |  | 0.00 €
 |  |  |  |  |  |  |  |  |  |  |  |  |  | 0.00 €
 |  |  |  |  |  |  |  |  |  |  |  |  |  | 0.00 €
 |  |  |  |  |  |  |  |  |  |  |  |  |  | 0.00 €
 |  |  |  |  |  |  |  |  |  |  |  |  |  | 0.00 €
 |  |  |  |  |  |  |  |  |  |  |  |  |  | 0.00 €
 |  |  |  |  |  |  |  |  |  |  |  |  |  | 0.00 €
 |  |  |  |  |  |  |  |  |  |  |  |  |  | 0.00 €
 |  |  |  |  |  |  |  |  |  |  |  |  |  | 0.00 €
 |  |  |  |  |  |  |  |  |  |  |  |  |  | 0.00 €
 |  |  |  |  |  |  |  |  |  |  |  |  |  | 0.00 €
 |  |  |  |  |  |  |  |  |  |  |  |  |  | 0.00 €
 |  |  |  |  |  |  |  |  |  |  |  |  |  | 0.00 €
 |  |  |  |  |  |  |  |  |  |  |  |  |  | 0.00 €
 |  |  |  |  |  |  |  |  |  |  |  |  |  | 0.00 €
 |  |  |  |  |  |  |  |  |  |  |  |  |  | 0.00 €
 |  |  |  |  |  |  |  |  |  |  |  |  |  | 0.00 €
 |  |  |  |  |  |  |  |  |  |  |  |  |  | 0.00 €
 |  |  |  |  |  |  |  |  |  |  |  |  |  | 0.00 €
 |  |  |  |  |  |  |  |  |  |  |  |  |  | 0.00 €
 |  |  |  |  |  |  |  |  |  |  |  |  |  | 0.00 €
 |  |  |  |  |  |  |  |  |  |  |  |  |  | 0.00 €
 |  |  |  |  |  |  |  |  |  |  |  |  |  | 0.00 €
 |  |  |  |  |  |  |  |  |  |  |  |  |  | 0.00 €
 |  |  |  |  |  |  |  |  |  |  |  |  |  | 0.00 €
 |  |  |  |  |  |  |  |  |  |  |  |  |  | 0.00 €
 |  |  |  |  |  |  |  |  |  |  |  |  |  | 0.00 €
 |  |  |  |  |  |  |  |  |  |  |  |  |  | 0.00 €
 |  |  |  |  |  |  |  |  |  |  |  |  |  | 0.00 €
 |  |  |  |  |  |  |  |  |  |  |  |  |  | 0.00 €
 |  |  |  |  |  |  |  |  |  |  |  |  |  | 0.00 €
 |  |  |  |  |  |  |  |  |  |  |  |  |  | 0.00 €
 |  |  |  |  |  |  |  |  |  |  |  |  |  | 0.00 €
 |  |  |  |  |  |  |  |  |  |  |  |  |  | 0.00 €
 |  |  |  |  |  |  |  |  |  |  |  |  |  | 0.00 €
 |  |  |  |  |  |  |  |  |  |  |  |  |  | 0.00 €
 |  |  |  |  |  |  |  |  |  |  |  |  |  | 0.00 €
 |  |  |  |  |  |  |  |  |  |  |  |  |  | 0.00 €
 |  |  |  |  |  |  |  |  |  |  |  |  |  | 0.00 €
 |  |  |  |  |  |  |  |  |  |  |  |  |  | 0.00 €
 |  |  |  |  |  |  |  |  |  |  |  |  |  | 0.00 €
 |  |  |  |  |  |  |  |  |  |  |  |  |  | 0.00 €
 |  |  |  |  |  |  |  |  |  |  |  |  |  | 0.00 €
 |  |  |  |  |  |  |  |  |  |  |  |  |  | 0.00 €
 |  |  |  |  |  |  |  |  |  |  |  |  |  | 0.00 €
 |  |  |  |  |  |  |  |  |  |  |  |  |  | 0.00 €
 |  |  |  |  |  |  |  |  |  |  |  |  |  | 0.00 €
 |  |  |  |  |  |  |  |  |  |  |  |  |  | 0.00 €
 |  |  |  |  |  |  |  |  |  |  |  |  |  | 0.00 €
 |  |  |  |  |  |  |  |  |  |  |  |  |  | 0.00 €
 |  |  |  |  |  |  |  |  |  |  |  |  |  | 0.00 €
 |  |  |  |  |  |  |  |  |  |  |  |  |  | 0.00 €
 |  |  |  |  |  |  |  |  |  |  |  |  |  | 0.00 €
 |  |  |  |  |  |  |  |  |  |  |  |  |  | 0.00 €
 |  |  |  |  |  |  |  |  |  |  |  |  |  | 0.00 €
 |  |  |  |  |  |  |  |  |  |  |  |  |  | 0.00 €
 |  |  |  |  |  |  |  |  |  |  |  |  |  | 0.00 €
 |  |  |  |  |  |  |  |  |  |  |  |  |  | 0.00 €
 |  |  |  |  |  |  |  |  |  |  |  |  |  | 0.00 €
 |  |  |  |  |  |  |  |  |  |  |  |  |  | 0.00 €
 |  |  |  |  |  |  |  |  |  |  |  |  |  | 0.00 €
 |  |  |  |  |  |  |  |  |  |  |  |  |  | 0.00 €
 |  |  |  |  |  |  |  |  |  |  |  |  |  | 0.00 €
 |  |  |  |  |  |  |  |  |  |  |  |  |  | 0.00 €
 |  |  |  |  |  |  |  |  |  |  |  |  |  | 0.00 €
 |  |  |  |  |  |  |  |  |  |  |  |  |  | 0.00 €
 |  |  |  |  |  |  |  |  |  |  |  |  |  | 0.00 €
 |  |  |  |  |  |  |  |  |  |  |  |  |  | 0.00 €
 |  |  |  |  |  |  |  |  |  |  |  |  |  | 0.00 €
 |  |  |  |  |  |  |  |  |  |  |  |  |  | 0.00 €
 |  |  |  |  |  |  |  |  |  |  |  |  |  | 0.00 €
 |  |  |  |  |  |  |  |  |  |  |  |  |  | 0.00 €
 |  |  |  |  |  |  |  |  |  |  |  |  |  | 0.00 €
 |  |  |  |  |  |  |  |  |  |  |  |  |  | 0.00 €
 |  |  |  |  |  |  |  |  |  |  |  |  |  | 0.00 €
 |  |  |  |  |  |  |  |  |  |  |  |  |  | 0.00 €
 |  |  |  |  |  |  |  |  |  |  |  |  |  | 0.00 €
 |  |  |  |  |  |  |  |  |  |  |  |  |  | 0.00 €
 |  |  |  |  |  |  |  |  |  |  |  |  |  | 0.00 €
 |  |  |  |  |  |  |  |  |  |  |  |  |  | 0.00 €
 |  |  |  |  |  |  |  |  |  |  |  |  |  | 0.00 €
 |  |  |  |  |  |  |  |  |  |  |  |  |  | 0.00 €
 |  |  |  |  |  |  |  |  |  |  |  |  |  | 0.00 €
 |  |  |  |  |  |  |  |  |  |  |  |  |  | 0.00 €
 |  |  |  |  |  |  |  |  |  |  |  |  |  | 0.00 €
 |  |  |  |  |  |  |  |  |  |  |  |  |  | 0.00 €
 |  |  |  |  |  |  |  |  |  |  |  |  |  | 0.00 €
 |  |  |  |  |  |  |  |  |  |  |  |  |  | 0.00 €
 |  |  |  |  |  |  |  |  |  |  |  |  |  | 0.00 €
 |  |  |  |  |  |  |  |  |  |  |  |  |  | 0.00 €
 |  |  |  |  |  |  |  |  |  |  |  |  |  | 0.00 €
 |  |  |  |  |  |  |  |  |  |  |  |  |  | 0.00 €
 |  |  |  |  |  |  |  |  |  |  |  |  |  | 0.00 €
 |  |  |  |  |  |  |  |  |  |  |  |  |  | 0.00 €
 |  |  |  |  |  |  |  |  |  |  |  |  |  | 0.00 €
 |  |  |  |  |  |  |  |  |  |  |  |  |  | 0.00 €
 |  |  |  |  |  |  |  |  |  |  |  |  |  | 0.00 €
 |  |  |  |  |  |  |  |  |  |  |  |  |  | 0.00 €
 |  |  |  |  |  |  |  |  |  |  |  |  |  | 0.00 €
 |  |  |  |  |  |  |  |  |  |  |  |  |  | 0.00 €
 |  |  |  |  |  |  |  |  |  |  |  |  |  | 0.00 €
 |  |  |  |  |  |  |  |  |  |  |  |  |  | 0.00 €
 |  |  |  |  |  |  |  |  |  |  |  |  |  | 0.00 €
 |  |  |  |  |  |  |  |  |  |  |  |  |  | 0.00 €
 |  |  |  |  |  |  |  |  |  |  |  |  |  | 0.00 €
 |  |  |  |  |  |  |  |  |  |  |  |  |  | 0.00 €
 |  |  |  |  |  |  |  |  |  |  |  |  |  | 0.00 €
 |  |  |  |  |  |  |  |  |  |  |  |  |  | 0.00 €
 |  |  |  |  |  |  |  |  |  |  |  |  |  | 0.00 €
 |  |  |  |  |  |  |  |  |  |  |  |  |  | 0.00 €
 |  |  |  |  |  |  |  |  |  |  |  |  |  | 0.00 €
 |  |  |  |  |  |  |  |  |  |  |  |  |  | 0.00 €
 |  |  |  |  |  |  |  |  |  |  |  |  |  | 0.00 €
 |  |  |  |  |  |  |  |  |  |  |  |  |  | 0.00 €
 |  |  |  |  |  |  |  |  |  |  |  |  |  | 0.00 €
 |  |  |  |  |  |  |  |  |  |  |  |  |  | 0.00 €
 |  |  |  |  |  |  |  |  |  |  |  |  |  | 0.00 €
 |  |  |  |  |  |  |  |  |  |  |  |  |  | 0.00 €
 |  |  |  |  |  |  |  |  |  |  |  |  |  | 0.00 €
 |  |  |  |  |  |  |  |  |  |  |  |  |  | 0.00 €
 |  |  |  |  |  |  |  |  |  |  |  |  |  | 0.00 €
 |  |  |  |  |  |  |  |  |  |  |  |  |  | 0.00 €
 |  |  |  |  |  |  |  |  |  |  |  |  |  | 0.00 €
 |  |  |  |  |  |  |  |  |  |  |  |  |  | 0.00 €
 |  |  |  |  |  |  |  |  |  |  |  |  |  | 0.00 €
 |  |  |  |  |  |  |  |  |  |  |  |  |  | 0.00 €
 |  |  |  |  |  |  |  |  |  |  |  |  |  | 0.00 €
 |  |  |  |  |  |  |  |  |  |  |  |  |  | 0.00 €
 |  |  |  |  |  |  |  |  |  |  |  |  |  | 0.00 €
 |  |  |  |  |  |  |  |  |  |  |  |  |  | 0.00 €
 |  |  |  |  |  |  |  |  |  |  |  |  |  | 0.00 €
 |  |  |  |  |  |  |  |  |  |  |  |  |  | 0.00 €
 |  |  |  |  |  |  |  |  |  |  |  |  |  | 0.00 €
 |  |  |  |  |  |  |  |  |  |  |  |  |  | 0.00 €
 |  |  |  |  |  |  |  |  |  |  |  |  |  | 0.00 €
 |  |  |  |  |  |  |  |  |  |  |  |  |  | 0.00 €
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

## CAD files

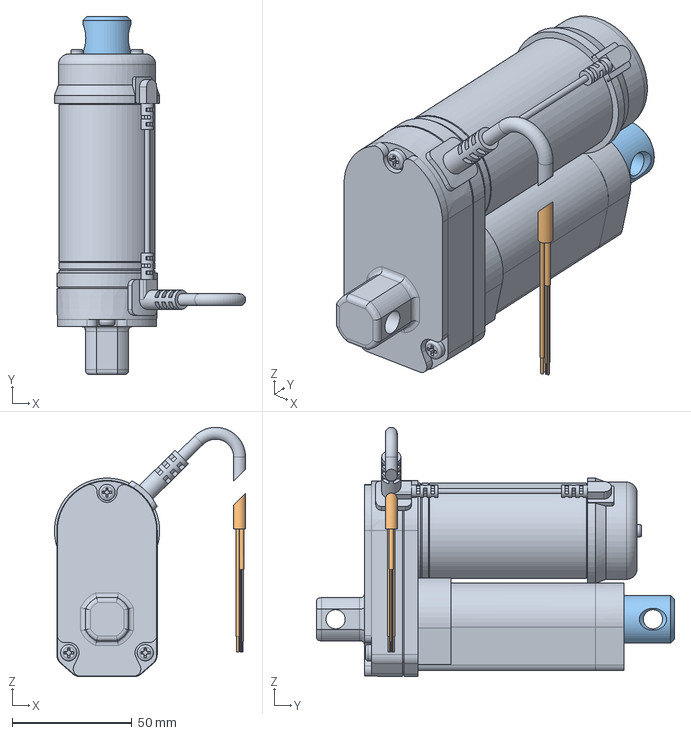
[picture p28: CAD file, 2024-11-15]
Projektarbeit_Hyperloop_cargopod/5_Datenblätter/3_Bremsen/Transmotec-Cad-DLA-X-X-A-25-HS2-IP65.stp
79.9 x 149.6 x 104.2 mm
DLA-X-X-A-25-HS2-IP65-1
DLA-X-X-A-25-HS2-IP65-2

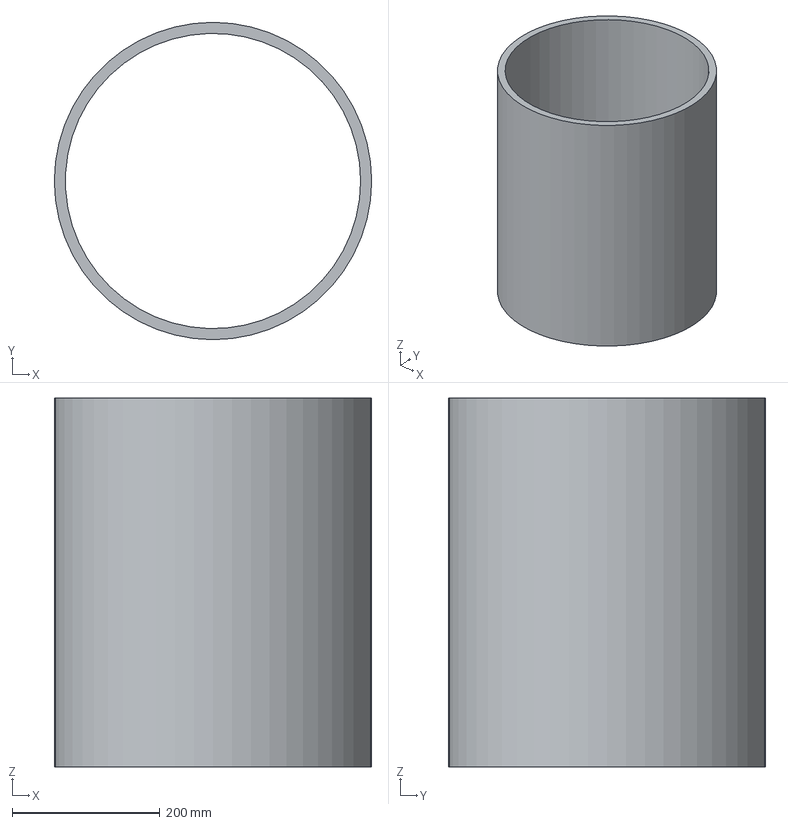
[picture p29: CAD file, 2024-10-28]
Zeichnungen/FreeCad/Schaltkasten/step/Zylinder-KörperPad.step
430.0 x 430.0 x 500.0 mm

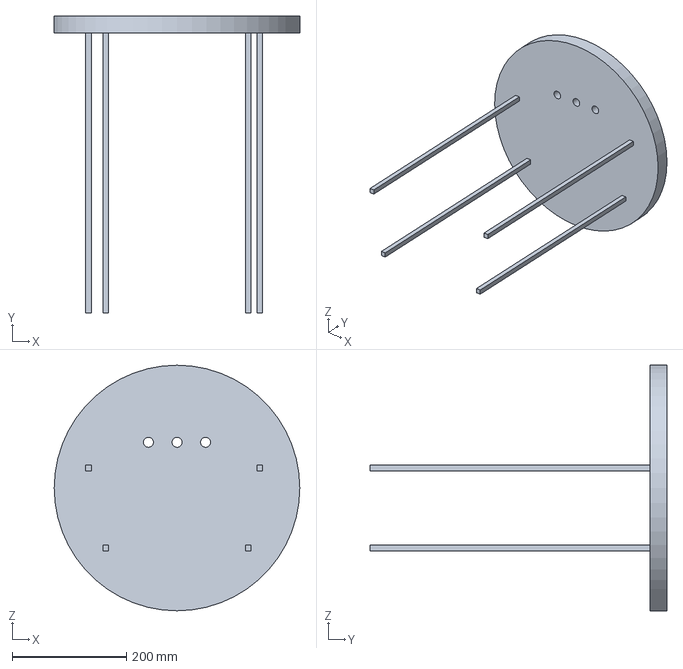
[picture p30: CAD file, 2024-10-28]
Zeichnungen/FreeCad/Schaltkasten/Tür.FCStd
430.0 x 520.0 x 430.0 mm

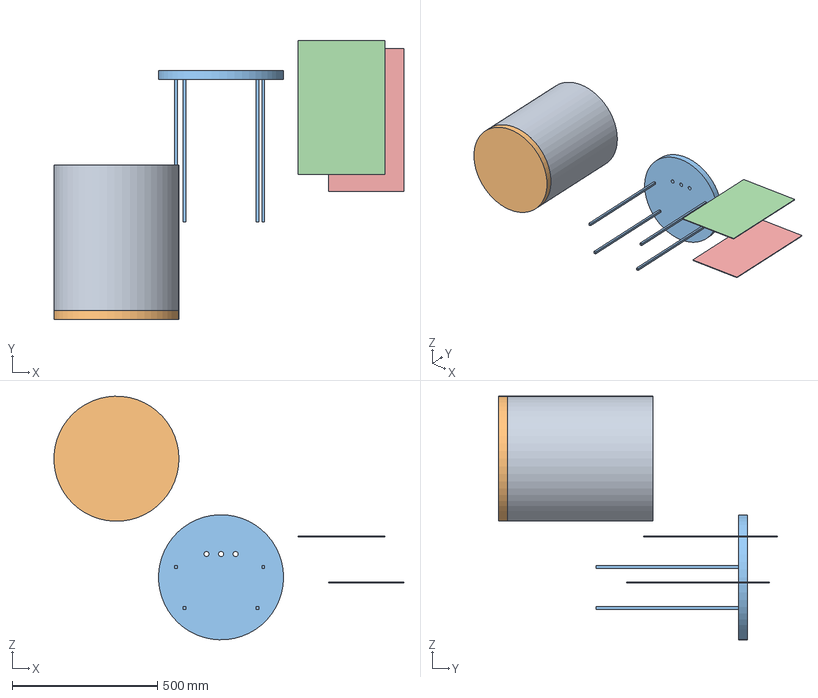
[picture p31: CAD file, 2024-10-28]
Zeichnungen/FreeCad/Schaltkasten_2/Schaltkasten.FCStd
1203.1 x 958.4 x 837.4 mm
Zylinder_001
Deckel_001
Tür_001
Platte_Oben_001
Platte_Unten_001

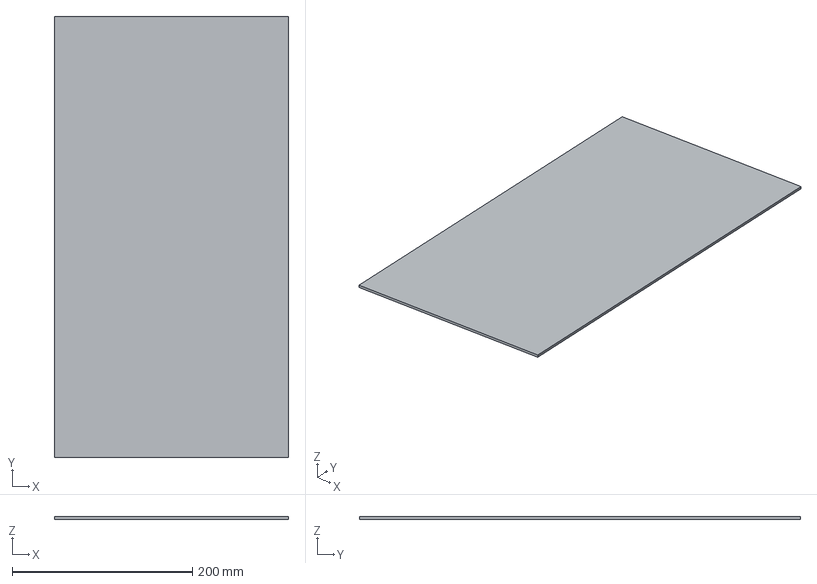
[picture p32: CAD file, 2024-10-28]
Zeichnungen/FreeCad/Schaltkasten/step/Platte_Unten-KörperPad.step
260.0 x 490.0 x 3.00 mm

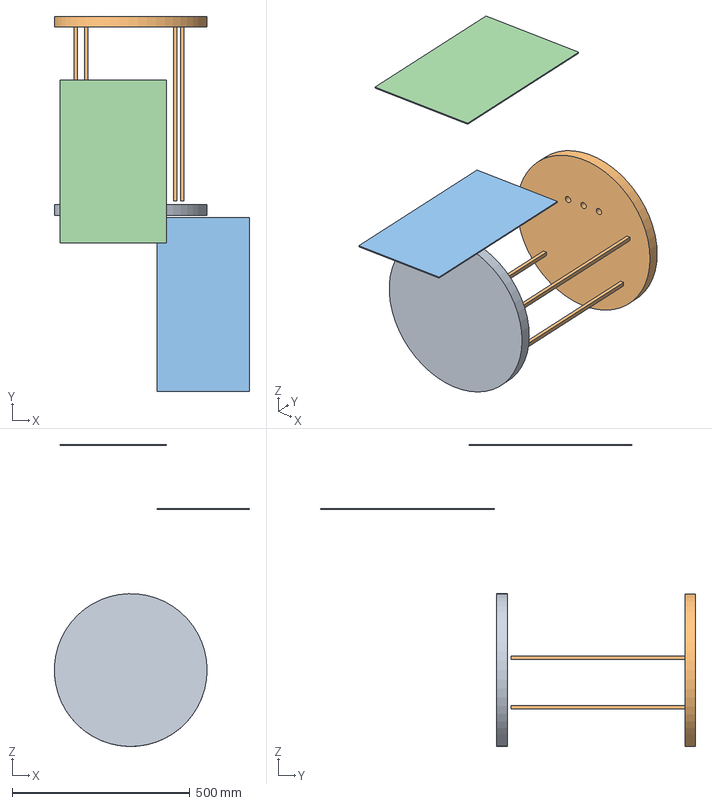
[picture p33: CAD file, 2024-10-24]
Zeichnungen/FreeCad/Schaltkasten/Schaltkasten.FCStd
549.0 x 1056.6 x 849.8 mm
Deckel_Deckel_001
Tür_Körper_001
Platte_Unten_Körper_001
Platte_Oben_Körper_001

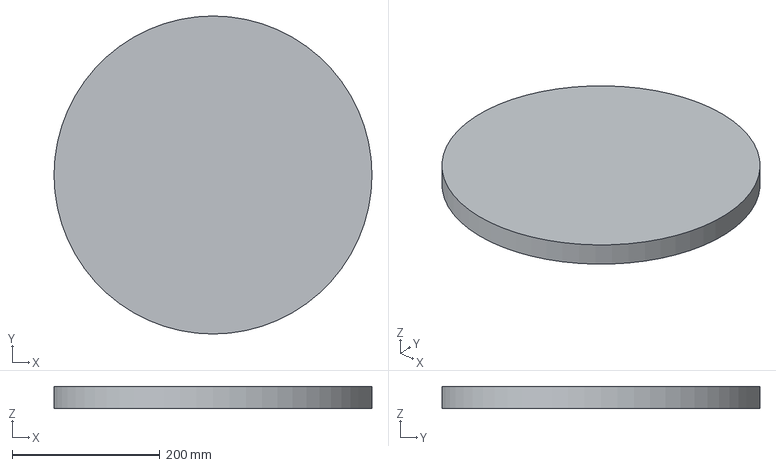
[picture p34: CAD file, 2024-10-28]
Zeichnungen/FreeCad/Schaltkasten/step/Deckel-DeckelPad_Deckel.step
430.0 x 430.0 x 30.0 mm

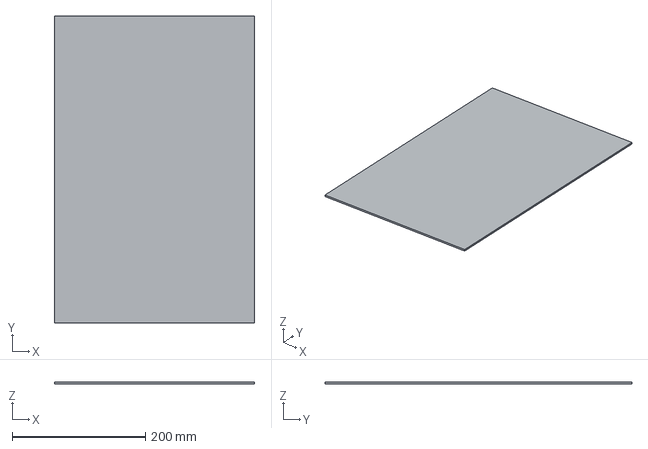
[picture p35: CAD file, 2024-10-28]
Zeichnungen/FreeCad/Schaltkasten/step/Platte_Oben-KörperPad.step
300.0 x 460.0 x 3.00 mm

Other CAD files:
Zeichnungen/FreeCad/Schaltkasten/Zylinder.FCStd
Zeichnungen/FreeCad/Schaltkasten/step/Tür-KörperHole.step
Zeichnungen/FreeCad/Schaltkasten/Platte_Unten.FCStd
Zeichnungen/FreeCad/Schaltkasten/Deckel.FCStd
Zeichnungen/FreeCad/Schaltkasten/Platte_Oben.FCStd

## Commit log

2024-04-14 Deckblatt ist vollständig Kapitel 1 ist Motivation und Aufgabenstellung vorhanden. Kapitel 2 ist angefangen.
2024-05-06 Schaltplan und matlab
2024-05-17 Not-Aus; Break ohne Pipen integriert und
2024-08-11 Bilder und texte
2024-08-12 Speedgoat wurde Tiefer erklärt und Golden Motor muss nur noch der Vektor Contoller erklärt werden
2024-08-16 Besprechung mit Yaman, wegen dem Distanzsensor und Notizen in Implem.
2024-09-12 Matlab V3 Controllpanel und Manueller betrieb sind hinzugefügt worden. Tex geht langsam weiter
2024-09-30 Abgabe bei Herr Schüning und Herr Neu
2024-10-24 automatische steuerung ist angefangen
    [Deckel.FCStd, Platte_Oben.FCStd, Platte_Unten.FCStd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]
2024-11-04 Anpassung von Okko und Schaltpaln
